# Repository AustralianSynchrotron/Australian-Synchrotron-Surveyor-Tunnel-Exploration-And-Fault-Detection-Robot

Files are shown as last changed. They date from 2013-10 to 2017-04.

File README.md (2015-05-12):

Australian-Synchrotron-Surveyor-Tunnel-Exploration-And-Fault-Detection-Robot
=======

Australian Synchrotron Tunnel Bot


###Requirements
------------

1. Python 2.7.x
2. ZeroMQ 3.2.x
3. pyzmq  13.1.0
4. Pyserial
5. libphidget LATEST (currently 2.1.8.20130723)
6. libusb 1.0-0
7. mjpg-streamer experimental
8. cherrypy 3.2.x
9. Arduino 1.5
-- PS2X by Bill Porter
10. supervisor 3.0b2-1
11. ROOter Huntsman 2014-01-25red

###Changes
-------

ipc doesn't seem to be working on this current configuration (except for LCD screen) so motors and IR Sensors using zmq on tcp://127.0.0.2
ports:
irsensor 127.0.0.2:1000
motors 127.0.0.2:1100

note: srv_motor.py now has the bind command for the motors zmq socket, since it is the service which is always running. If testing run py script with sudo

###Command Line
--------

ssh to odroid. The following command line scripts can be used for some low level control of ass-bot

**move** *\<direction\> \<duration\> \<speed\>*

* direction: forward (f), back (b), left (l), right (r)

* duration: time of movement in seconds

* speed: percentage of max speed. From 1 to 100

**shaft** *\<direction\> \<duration\>*

* direction: up (u) or down (d)

* duration: time of movement in seconds

**camera** *\<direction\> \<PWM duration\>*

* direction: Pan (p) or tilt (t)

* PWM duration: Pulse width from 500 to 2500. Form tilt centre value is 900, for pan centre value is 1500

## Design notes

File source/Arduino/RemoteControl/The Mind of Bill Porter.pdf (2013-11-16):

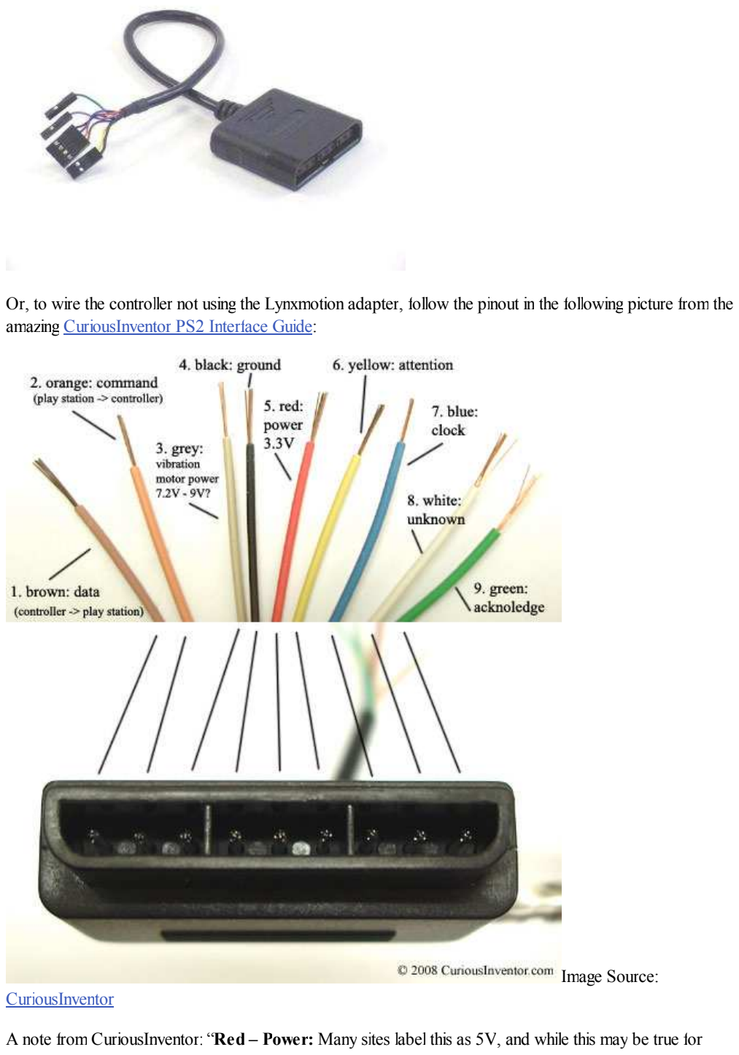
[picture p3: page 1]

Or, to wire the controller not using the Lynxmotion adapter, follow the pinout in the following picture from the amazing CuriousInventor PS2 Interface Guide:

Image Source:
CuriousInventor
A note from CuriousInventor: “Red – | Power: | Many sites label this as 5V, and while this may be true for

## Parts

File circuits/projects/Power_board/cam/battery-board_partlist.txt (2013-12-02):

Partlist

Exported from battery_board.brd at 2/12/2013 4:05:52 PM

EAGLE Version 6.4.0 Copyright (c) 1988-2013 CadSoft

Assembly variant: 

Part         Value           Package              Library  Position (mil)        Orientation

BATT1_V      1-HOLE          1-HOLE_BIG           parts    (3250 3200)           R0
BATT2_V      1-HOLE          1-HOLE_BIG           parts    (2450 3200)           R0
BATTERY1     12V             SCREWTERMINAL-5MM-2  parts    (3900 3600)           R180
BATTERY2     12V             SCREWTERMINAL-5MM-2  parts    (3050 3600)           R180
C1           10uF            C050-024X044         parts    (875 2250)            R180
C2           2.2uF           C050-024X044         parts    (875 2750)            R180
CHARGER      24V             SCREWTERMINAL-5MM-2  parts    (4950 3600)           R180
CHARGE_ON    1-HOLE          1-HOLE_BIG           parts    (5150 2875)           R0
D1           BZX55           DO35Z10              parts    (4500 2350)           R0
D1-12V       30A             TO22-DIODE-H         parts    (3650 1150)           R270
D2-12V       30A             TO22-DIODE-H         parts    (1500 3325)           R270
D3-24V       30A             TO22-DIODE-H         parts    (2500 1150)           R270
FUSE-M1      3A              SCREWTERMINAL-5MM-2  parts    (375 1300)            R270
FUSE-M2      3A              SCREWTERMINAL-5MM-2  parts    (375 1775)            R270
LED-12V                      LED5MM               parts    (5150 1800)           R0
LED-24V                      LED5MM               parts    (5150 1450)           R0
LED-CHARGE                   LED5MM               parts    (5150 2550)           R0
LED-CHARGING                 LED5MM               parts    (5150 2150)           R0
MOBO+5V      2-HOLESSC3.81MM SCREWTERMINAL-3.81MM parts    (250 2550)            R270
MOTOR-1      2-HOLESSC5MM    SCREWTERMINAL-5MM-2  parts    (1850 300)            R0
MOTOR-2      2-HOLESSC5MM    SCREWTERMINAL-5MM-2  parts    (950 300)             R0
OUTPUT       3-HOLE          SCREWTERMINAL-5MM-3  parts    (3500 250)            R0
R1           560R            0309/15              parts    (4600 2150)           R180
R2           1k              0309/15              parts    (4600 1450)           R0
R3           560R            0309/15              parts    (4600 1800)           R0
R4           1k              0309/15              parts    (4600 2875)           R180
R5           220R            0309/15              parts    (4600 2550)           R180
RELAY        5V              RELAY_RT2            parts    (2750 2200)           R180
RELAY_ON     1-HOLE          1-HOLE_BIG           parts    (3250 2575)           R0
VR-MB        LT323A          TO220V-HEATSINK      parts    (1425 2500)           R270

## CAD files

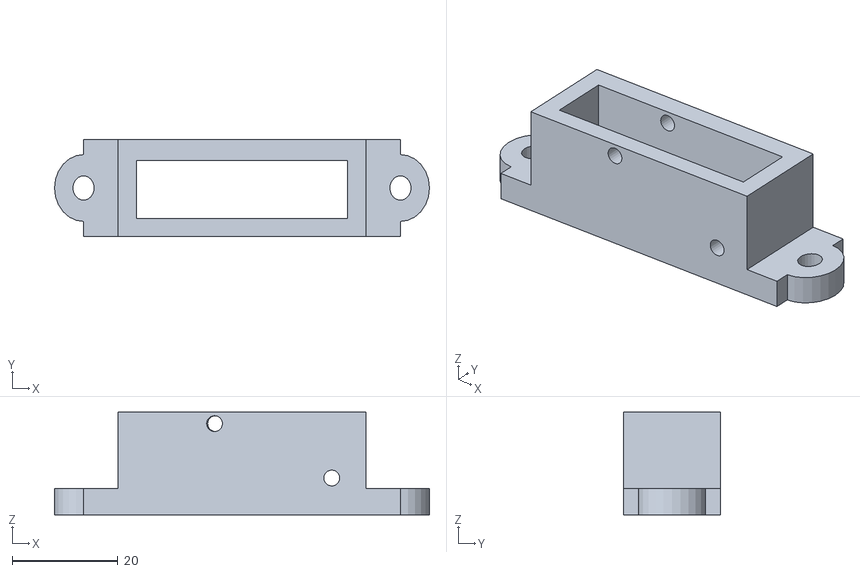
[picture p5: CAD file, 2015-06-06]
drawings/3D_Parts/switch-holder.stl
71.0 x 18.4 x 19.5

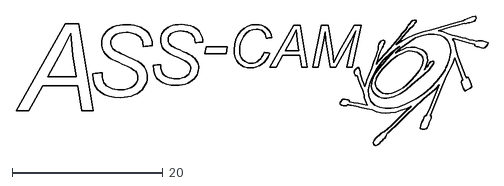
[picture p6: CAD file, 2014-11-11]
drawings/logos/asscam_logo-outline-small.dxf
62.6 x 17.2

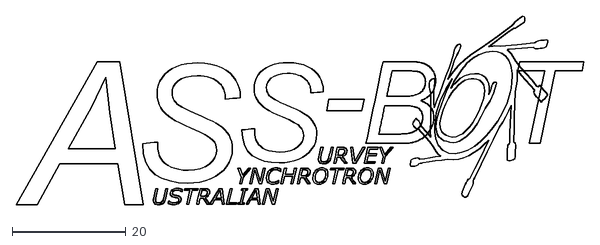
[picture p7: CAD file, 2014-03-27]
drawings/logos/assbot_logo-outline-small.dxf
99.9 x 33.1

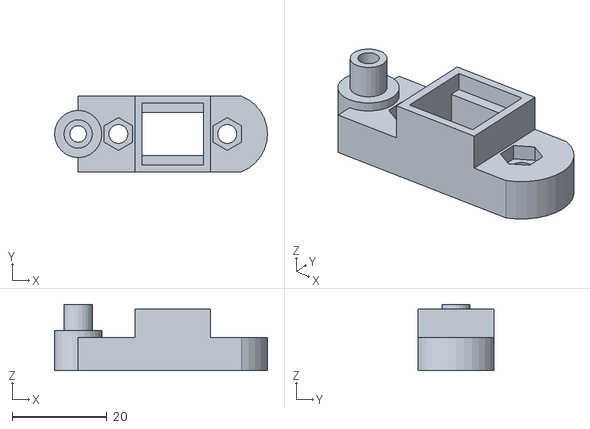
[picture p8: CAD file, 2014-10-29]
drawings/3D_Parts/switch_holder-single.stl
45.0 x 16.0 x 14.0

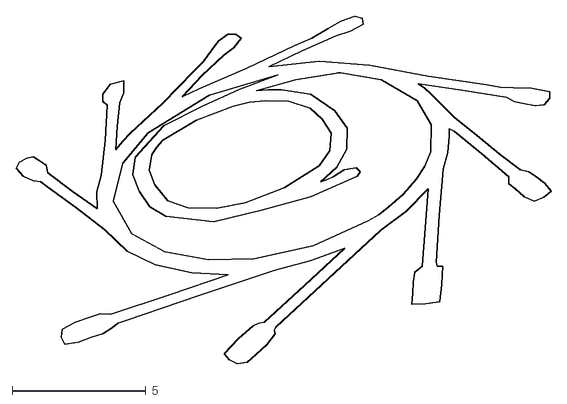
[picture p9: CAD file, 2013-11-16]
drawings/logos/synch-logo-small.dxf
20.0 x 13.0

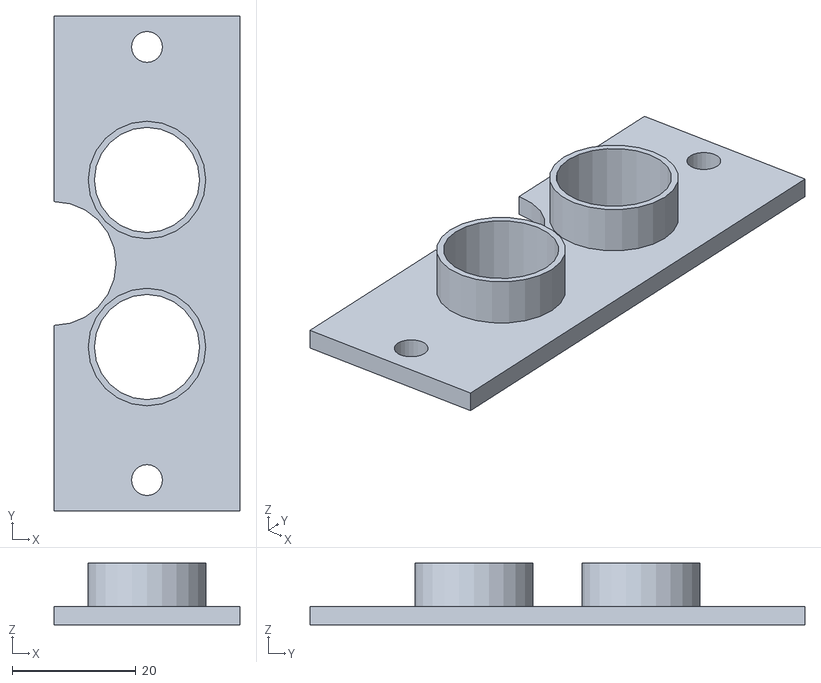
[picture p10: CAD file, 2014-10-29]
drawings/3D_Parts/Ultrasound-mount-cutaway.stl
30.0 x 80.0 x 10.00

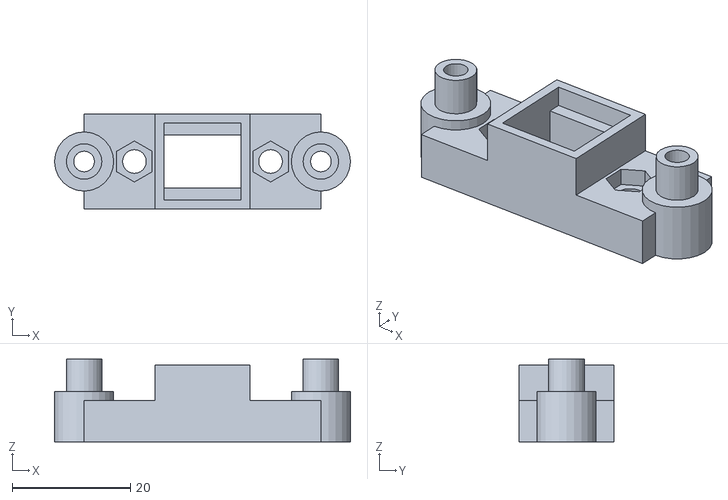
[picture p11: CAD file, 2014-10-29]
drawings/3D_Parts/switch_holder-double.stl
50.0 x 16.0 x 14.0

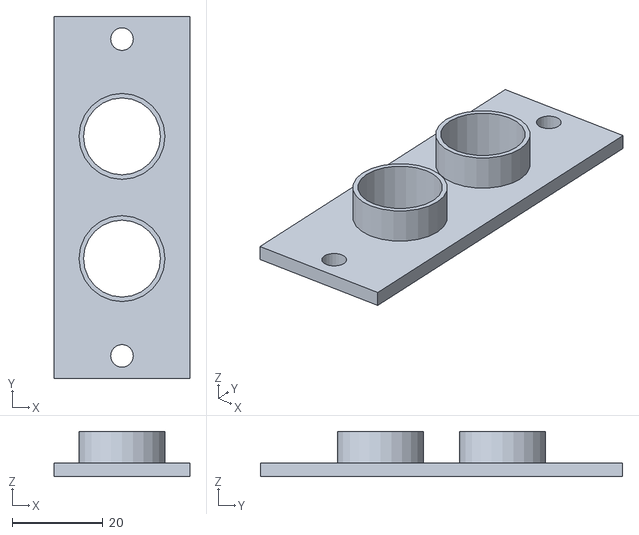
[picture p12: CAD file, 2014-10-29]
drawings/3D_Parts/Ultrasound-mount.stl
30.0 x 80.0 x 10.00

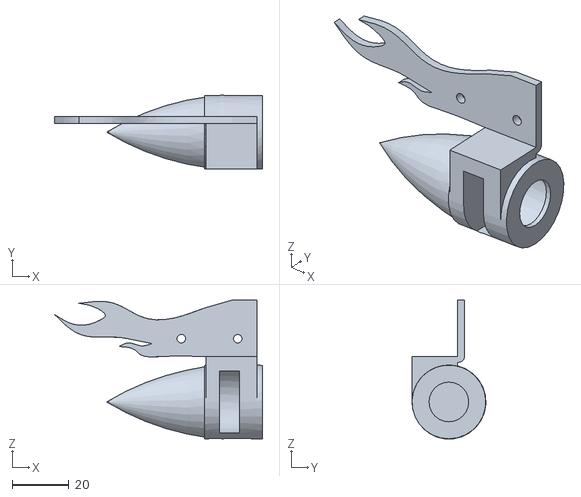
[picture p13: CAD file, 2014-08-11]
drawings/3D_Parts/SnapMagnetV2_Normal.stl
73.4 x 26.1 x 49.0

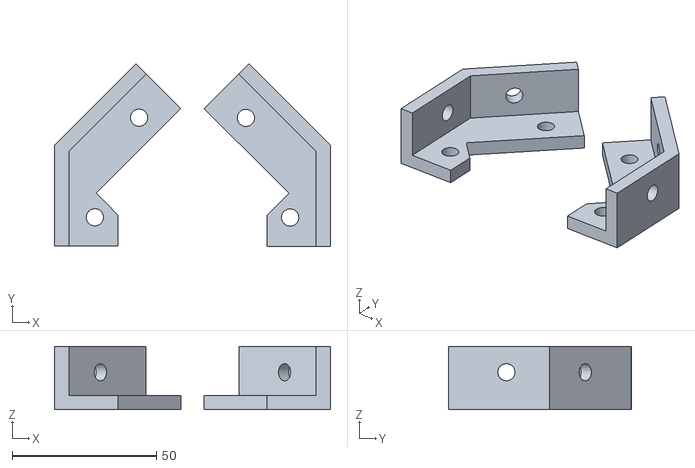
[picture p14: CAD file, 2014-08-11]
drawings/3D_Parts/corner-45deg-back-back.stl
95.7 x 63.4 x 22.0

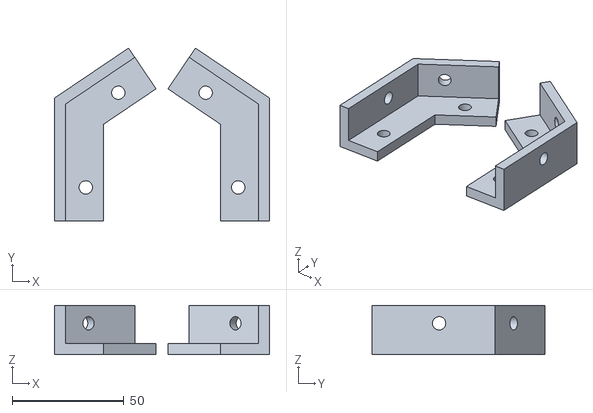
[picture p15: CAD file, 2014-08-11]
drawings/3D_Parts/Corner_pair-36deg.stl
96.2 x 77.4 x 22.0

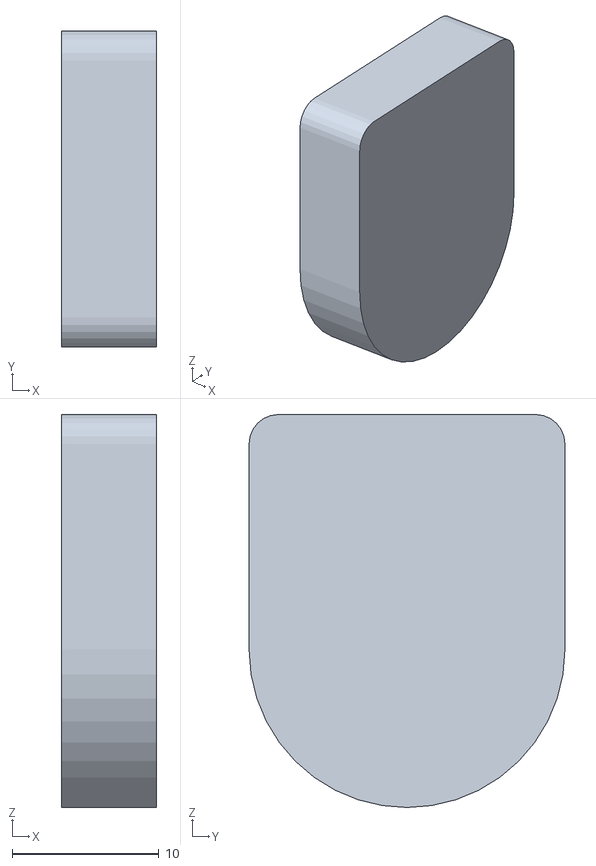
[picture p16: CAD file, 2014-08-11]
drawings/3D_Parts/SnapMagnet_Cork.stl
6.50 x 21.5 x 26.8

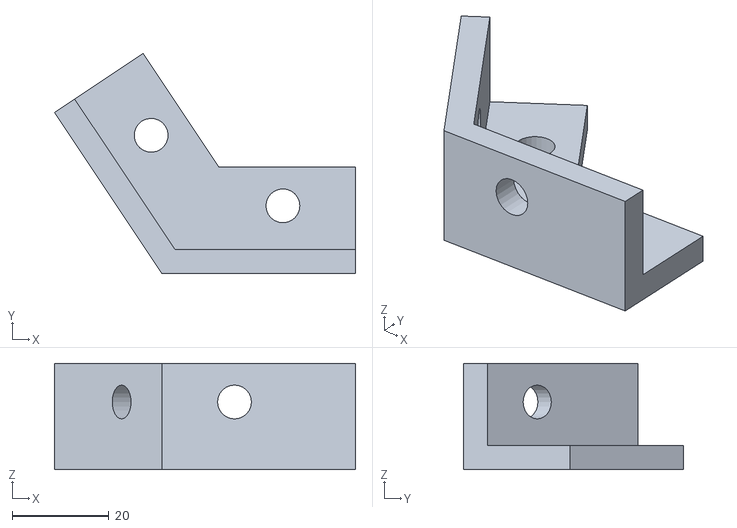
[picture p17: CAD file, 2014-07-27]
drawings/3D_Parts/corner_join_56.stl
62.2 x 45.5 x 22.0

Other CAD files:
drawings/Design/Cover Pieces ACAD2010.dwg
drawings/3D_Parts/Top_Plate_Concept.dwg
drawings/3D_Parts/PanTilt_Metal.dwg
drawings/3D_Parts/SnapMagnetV2_Goofy.stl
drawings/3D_Parts/SnapMagnet.dwg
drawings/3D_Parts/12mm-square-quadangle.skp
drawings/3D_Parts/12mm-square-tripleangle_left.skp
drawings/3D_Parts/12mm-square-tripleangle_left.stl
drawings/3D_Parts/12mm-square-tripleangle_right.skp
drawings/3D_Parts/12mm-square-tripleangle_right.stl
drawings/3D_Parts/20-210-M4-Extrusion.stl
drawings/3D_Parts/20-25angle-bracket-cutaway_left.skp
drawings/3D_Parts/20-25angle-bracket-cutaway_left.stl
drawings/3D_Parts/20-25angle-bracket-cutaway_right.skp
drawings/3D_Parts/20-25angle-bracket-cutaway_right.stl
drawings/3D_Parts/20-25angle-bracket.skp
drawings/3D_Parts/20-M4-connector.stl
drawings/3D_Parts/Calibration.stl
drawings/3D_Parts/Calibration2.stl
drawings/3D_Parts/Fan_Clip.dwg
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

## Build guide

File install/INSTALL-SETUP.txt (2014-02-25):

sudo dpkg-reconfigure tzdata
sudo apt-get remove chrome gimp xbmc
sudo apt-get autoremove
cd ~
mkdir GitHub
cd GitHub
git clone https://github.com/AustralianSynchrotron/Australian-Synchrotron-Surveyor-Tunnel-Exploration-And-Fault-Detection-Robot.git ./ass-bot
cd ~
sudo apt-get install libzmq3 libzmq3-dev
sudo apt-get install python-pip python2.7-dev
sudo pip install pyzmq
sudo apt-get install libusb-1.0-0-dev
mkdir phidgets
cd phidgets
wget http://www.phidgets.com/downloads/libraries/libphidget.tar.gz
tar -zxvf libphidget.tar.gz
cd libphidget-2.1.8.20130723/
./configure
make
sudo make install
wget http://www.phidgets.com/downloads/libraries/PhidgetsPython.zip
unzip PhidgetsPython.zip
cd PhidgetsPython/
sudo python setup.py install
cd ~
sudo pip install cherrypy
*************************************************************************
*  http://forum.odroid.com/viewtopic.php?f=21&t=20
*  Slow network Errors... smsc95xx eth0: kevent 2 may have been dropped
sudo echo 'vm.min_free_kbytes = 65536' >> /etc/sysctl.conf
sudo sysctl -p
sudo echo 'smsc95xx turbo_mode=N' >> /etc/modules 
*************************************************************************
sudo apt-get install subversion libv4l-dev libjpeg8-dev imagemagick
mkdir mjpeg-streamer
svn checkout svn://svn.code.sf.net/p/mjpg-streamer/code/
cd code/mjpg-streamer-experimental/
make USE_LIBV4L2=true clean all
sudo make DESTDIR=/usr install
sudo apt-get install sysstat

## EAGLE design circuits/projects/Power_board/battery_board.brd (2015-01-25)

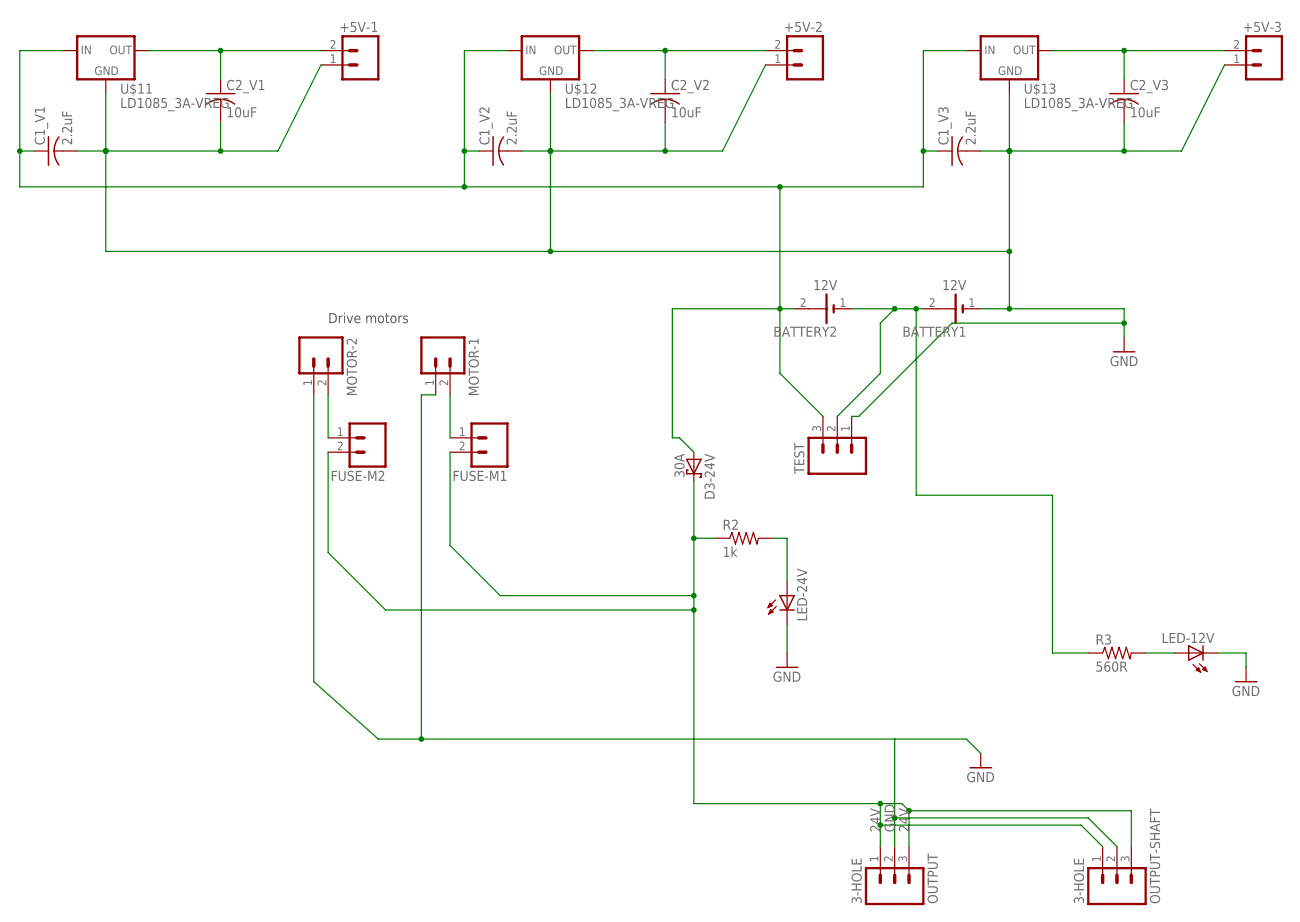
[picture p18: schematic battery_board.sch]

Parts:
+5V-1, +5V-2, +5V-3: 2-HOLESSC3.81MM; SCREWTERMINAL-3.81MM
BATTERY1, BATTERY2: 12V; SCREWTERMINAL-5MM-2
C1_V1, C1_V2, C1_V3: 2.2uF; C050-024X044
C2_V1, C2_V2, C2_V3: 10uF; C050-024X044
D3-24V: 30A; TO22-DIODE-H
FUSE-M1, FUSE-M2: 3A; SCREWTERMINAL-5MM-2
LED-12V, LED-24V: LED-5MM; LED5MM
MOTOR-1, MOTOR-2: 2-HOLESSC5MM; SCREWTERMINAL-5MM-2
OUTPUT: 3-HOLE; SCREWTERMINAL-5MM-3@1
OUTPUT-SHAFT: 3-HOLE; SCREWTERMINAL-5MM-3@1
R2: 1k; 0309/15
R3: 560R; 0309/15
TEST: M03PTH; 1X03
U$11, U$12, U$13: LD1085_3A-VREG; TO220V-HEATSINK2

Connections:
12V: BATTERY2.2 (+), C1_V1.1, C1_V2.1, C1_V3.1, D3-24V.P$1 (A), TEST.3, U$11.3 (IN), U$12.3 (IN), U$13.3 (IN)
24V: D3-24V.P$2 (C), FUSE-M1.2, FUSE-M2.2, OUTPUT.1, OUTPUT.3, OUTPUT-SHAFT.1, OUTPUT-SHAFT.3, R2.1
GND: +5V-1.1, +5V-2.1, +5V-3.1, BATTERY1.1 (-), C1_V1.2, C1_V2.2, C1_V3.2, C2_V1.2, C2_V2.2, C2_V3.2, LED-12V.K (C), LED-24V.K (C), MOTOR-1.1, MOTOR-2.1, OUTPUT.2, OUTPUT-SHAFT.2, TEST.1, U$11.1 (GND), U$12.1 (GND), U$13.1 (GND)
unnamed: LED-24V.A, R2.2
unnamed: BATTERY1.2 (+), BATTERY2.1 (-), R3.1, TEST.2
unnamed: +5V-3.2, C2_V3.1, U$13.2 (OUT)
unnamed: FUSE-M2.1, MOTOR-2.2
unnamed: FUSE-M1.1, MOTOR-1.2
unnamed: LED-12V.A, R3.2
unnamed: +5V-2.2, C2_V2.1, U$12.2 (OUT)
unnamed: +5V-1.2, C2_V1.1, U$11.2 (OUT)

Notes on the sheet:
Drive motors

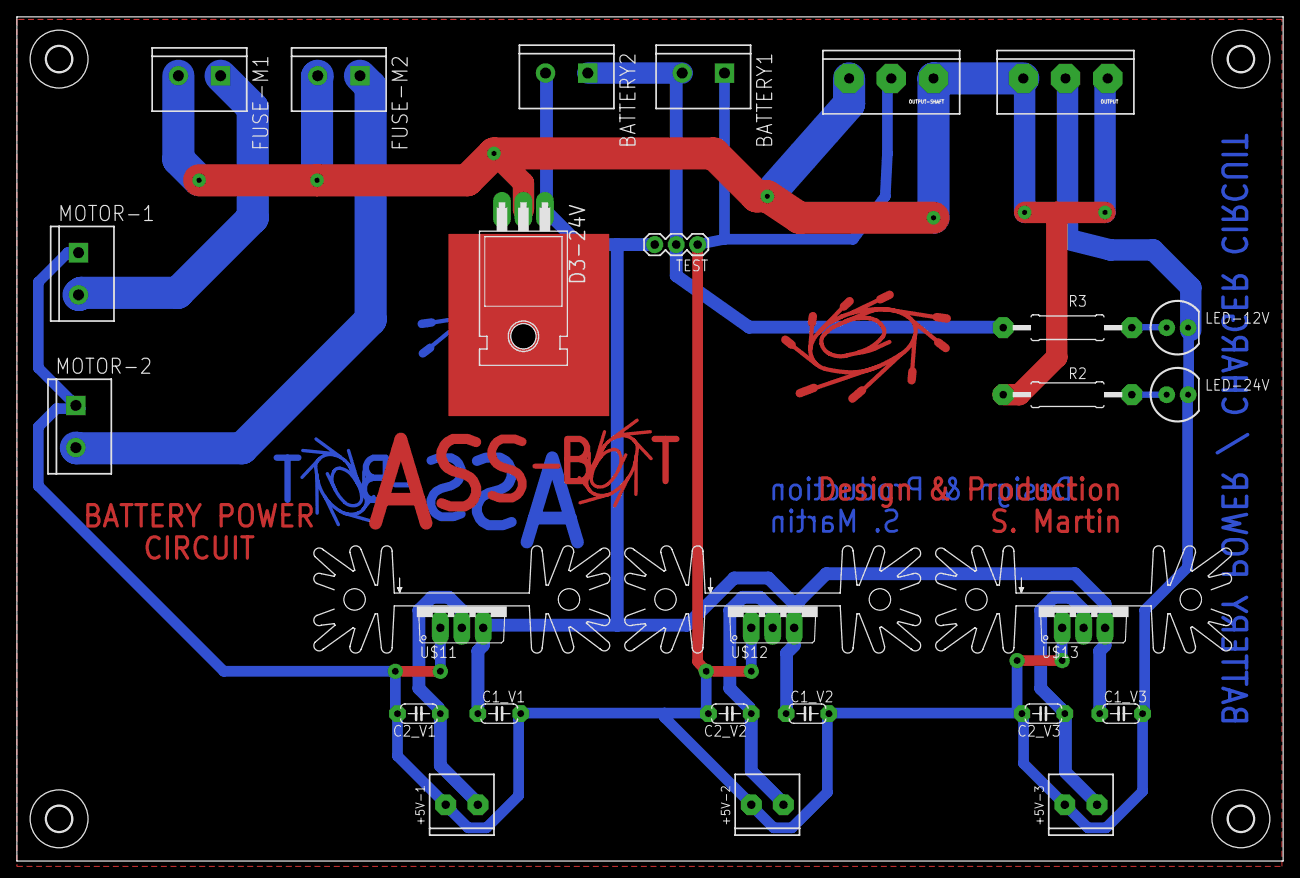
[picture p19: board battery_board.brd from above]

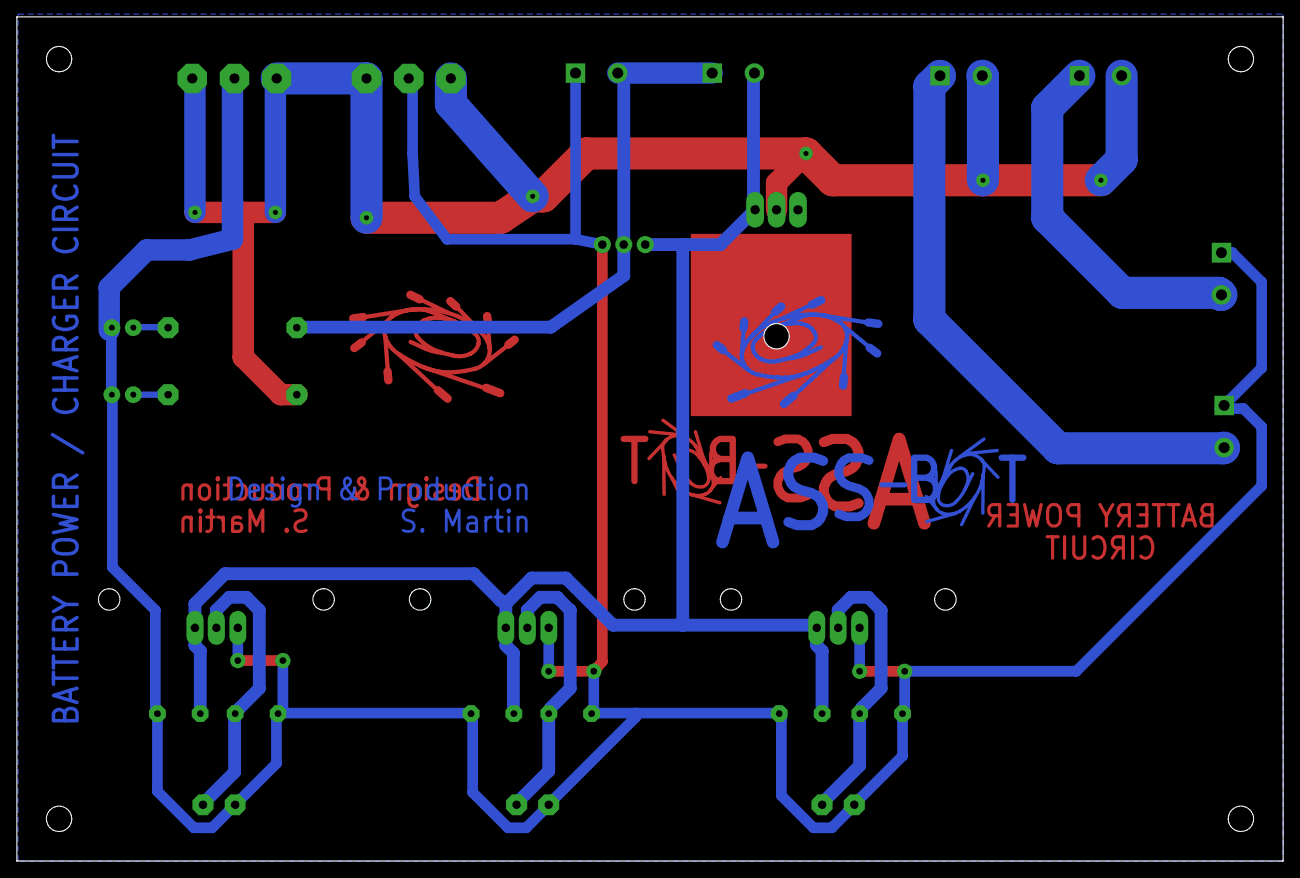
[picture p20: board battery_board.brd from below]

Board: 2 copper layers, 150.0 x 100.0 mm, 36 parts (2 on the bottom side), 11 nets.

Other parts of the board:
U$1, U$8: LOGO-SYNCHROTRON
U$2: LOGO-ASSBOT-SILK
U$3, U$4, U$5, U$6: 3,0
U$7, U$9: LOGO-ASSBOT
U$10: LOGO-SYNCHROTRON-SILK

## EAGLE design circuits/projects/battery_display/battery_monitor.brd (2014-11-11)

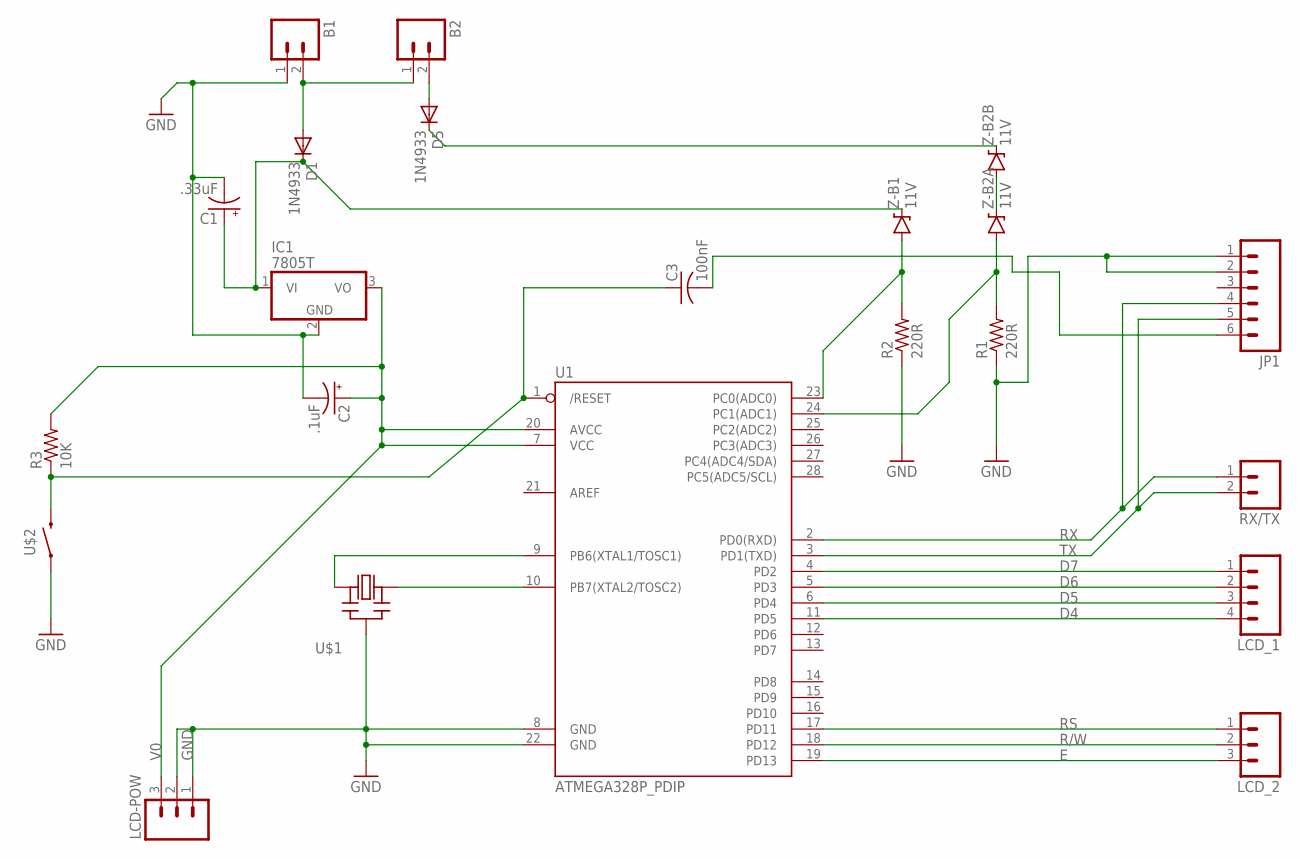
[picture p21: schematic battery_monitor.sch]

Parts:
B1, B2: 2-HOLES2-HOLES-5.08MM; 2-HOLES_BIG
C1: .33uF; E2,5-5
C2: .1uF; E2,5-5
C3: 100nF; C050-025X075
D1, D5: 1N4933; DO41-10
IC1: 7805T; TO220H
JP1: M06LONGPADS; 1X06_LONGPADS
LCD-POW: M03PTH; 1X03
LCD_1: M04PTH; 1X04
LCD_2: M03PTH; 1X03
R1, R2: 220R; 0207/10
R3: 10K; 0207/10
RX/TX: M02PTH; 1X02
U1: ATMEGA328P_PDIP; DIL28-3
U$1: OSCILLATOR-THM; CERM_OSC
U$2: SWITCH-MOMENTARY4MM; TACTILE_SWITCH_SMD
Z-B1, Z-B2A, Z-B2B: 11V; DIODE-ZENER

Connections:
D4: LCD_1.4, U1.11 (PD5)
D5: LCD_1.3, U1.6 (PD4)
D6: LCD_1.2, U1.5 (PD3)
D7: LCD_1.1, U1.4 (PD2)
E: LCD_2.3, U1.19 (PD13)
GND: B1.1, C1.-, C2.-, IC1.2 (GND), JP1.1, JP1.2, LCD-POW.1, LCD-POW.2, R1.1, R2.1, U1.8 (GND), U1.22 (GND), U$1.P$2 (GND), U$2.1, U$2.2 (1)
unnamed: U1.10 (PB7(XTAL2/TOSC2)), U$1.P$3 (OUT)
unnamed: U1.9 (PB6(XTAL1/TOSC1)), U$1.P$1 (IN)
unnamed: B1.2, B2.1, D1.A
unnamed: C1.+, D1.C, IC1.1 (VI), Z-B1.P$1 (C)
unnamed: Z-B2A.P$1 (C), Z-B2B.P$2 (A)
unnamed: C3.1, R3.1, U1.1 (/RESET), U$2.3 (2), U$2.4 (2)
unnamed: C3.2, JP1.6
unnamed: R2.2, U1.23 (PC0(ADC0)), Z-B1.P$2 (A)
unnamed: R1.2, U1.24 (PC1(ADC1)), Z-B2A.P$2 (A)
unnamed: D5.C, Z-B2B.P$1 (C)
unnamed: B2.2, D5.A
R/W: LCD_2.2, U1.18 (PD12)
RS: LCD_2.1, U1.17 (PD11)
RX: JP1.4, RX/TX.1, U1.2 (PD0(RXD))
TX: JP1.5, RX/TX.2, U1.3 (PD1(TXD))
V0: C2.+, IC1.3 (VO), LCD-POW.3, R3.2, U1.7 (VCC), U1.20 (AVCC)

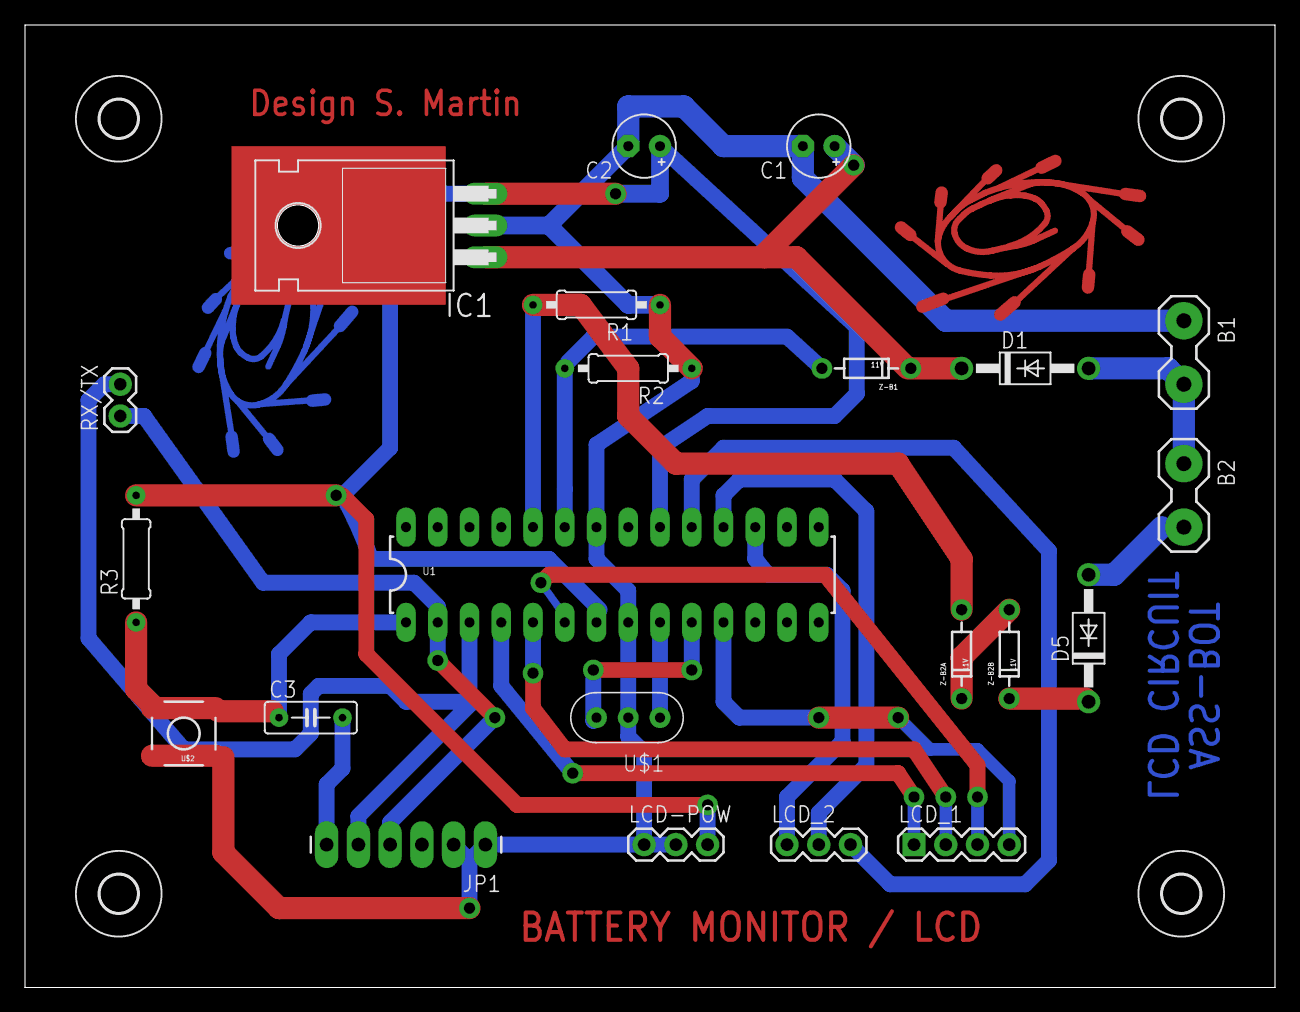
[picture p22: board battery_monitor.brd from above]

Board: 2 copper layers, 100.0 x 77.0 mm, 28 parts (1 on the bottom side), 22 nets.

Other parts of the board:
U$3, U$4, U$5, U$6: 3,0
U$7, U$8: LOGO-SYNCHROTRON

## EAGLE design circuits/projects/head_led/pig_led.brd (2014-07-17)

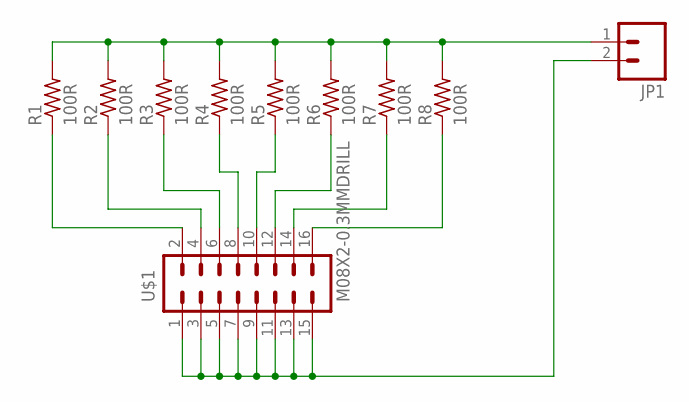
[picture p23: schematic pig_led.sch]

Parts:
JP1: M023.5MM; SCREWTERMINAL-3.5MM-2
R1, R2, R3, R4, R5, R6, R7, R8: 100R; 0207/10
U$1: M08X2-0.3MMDRILL; 2X8

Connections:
GND: JP1.2, U$1.1, U$1.3, U$1.5, U$1.7, U$1.9, U$1.11, U$1.13, U$1.15
unnamed: R1.1, U$1.2
unnamed: R2.1, U$1.4
unnamed: R3.1, U$1.6
unnamed: R4.1, U$1.8
unnamed: R5.1, U$1.10
unnamed: R6.1, U$1.12
unnamed: R7.1, U$1.14
unnamed: R8.1, U$1.16
VCC: JP1.1, R1.2, R2.2, R3.2, R4.2, R5.2, R6.2, R7.2, R8.2

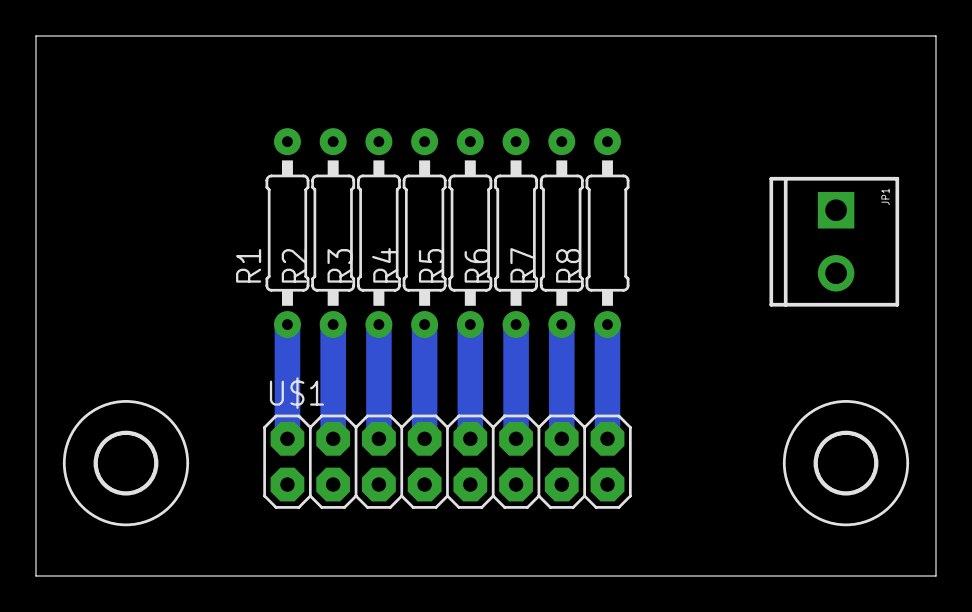
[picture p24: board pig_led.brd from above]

Board: 2 copper layers, 50.0 x 30.0 mm, 12 parts (0 on the bottom side), 10 nets.

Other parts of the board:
U$2, U$3: 3,2

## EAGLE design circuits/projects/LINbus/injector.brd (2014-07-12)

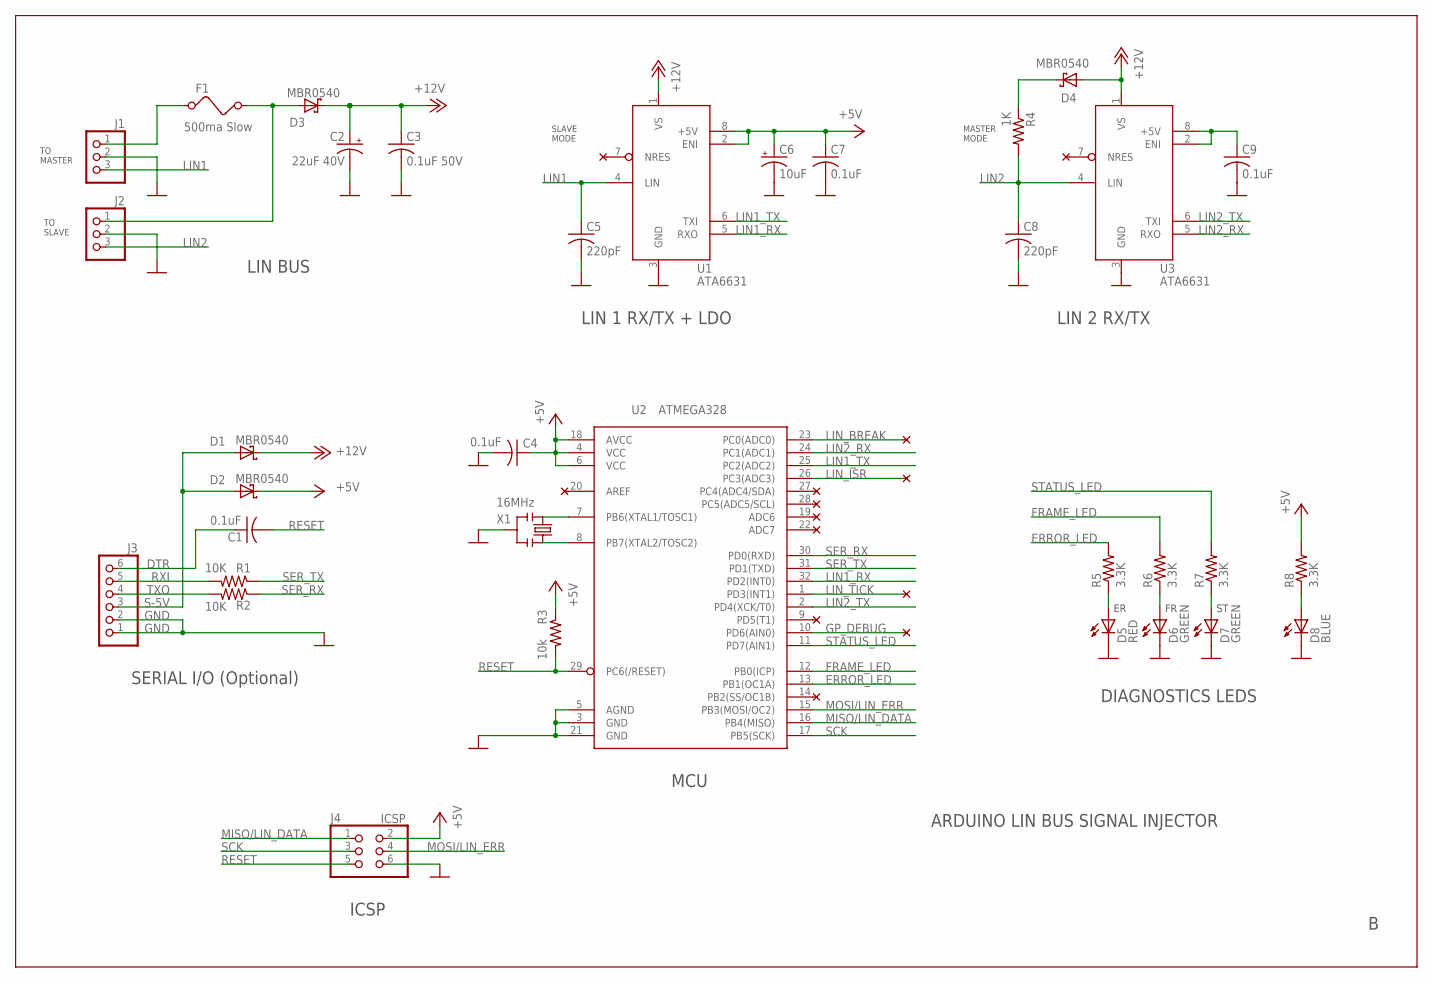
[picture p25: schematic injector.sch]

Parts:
C1, C4, C7, C9: 0.1uF; C0805
C2: 22uF 40V; UD-6,3X5,8_NICHICON
C3: 0.1uF 50V; C0805
C5, C8: 220pF; C0805
C6: 10uF; A/3216-18R
D1, D2, D3, D4: MBR0540; SOD123FL
D5: RED; 1206-LED
D6, D7: GREEN; 1206-LED
D8: BLUE; 1206-LED
F1: 500ma Slow; 1206
J1, J2: PINHD-1X3; 1X03
J3: PINHD-1X6; 1X06
J4: ICSP; 2X03
R1, R2: 10K; R0805
R3: 10k; R0805
R4: 1K; R0805
R5, R6, R7, R8: 3.3K; R0805
U1, U3: ATA6631; SO-08
U2: ATMEGA328; TQFP32-08
X1: 16MHz; RESONATOR-SMD

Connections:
+5V: C4.1, C6.+, C7.1, D2.C, J4.2, R3.1, R8.2, U1.2 (ENI), U1.8 (+5V), U2.4 (VCC), U2.6 (VCC), U2.18 (AVCC)
+12V: C2.+, C3.1, D1.C, D3.C, D4.A, U1.1 (VS), U3.1 (VS)
DTR: C1.1, J3.6
ERROR_LED: R5.2, U2.13 (PB1(OC1A))
FRAME_LED: R6.2, U2.12 (PB0(ICP))
GND: C2.-, C3.2, C4.2, C5.2, C6.-, C7.2, C8.2, C9.2, D5.C, D6.C, D7.C, D8.C, J1.2, J2.2, J3.1, J3.2, J4.6, U1.3 (GND), U2.3 (GND), U2.5 (AGND), U2.21 (GND), U3.3 (GND), X1.2
GP_DEBUG: U2.10 (PD6(AIN0))
LIN1: C5.1, J1.3, U1.4 (LIN)
LIN1_RX: U1.5 (RXO), U2.32 (PD2(INT0))
LIN1_TX: U1.6 (TXI), U2.25 (PC2(ADC2))
LIN2: C8.1, J2.3, R4.2, U3.4 (LIN)
LIN2_RX: U2.24 (PC1(ADC1)), U3.5 (RXO)
LIN2_TX: U2.2 (PD4(XCK/T0)), U3.6 (TXI)
LIN_BREAK: U2.23 (PC0(ADC0))
LIN_ISR: U2.26 (PC3(ADC3))
LIN_TICK: U2.1 (PD3(INT1))
MISO/LIN_DATA: J4.1, U2.16 (PB4(MISO))
MOSI/LIN_ERR: J4.4, U2.15 (PB3(MOSI/OC2))
unnamed: D7.A, R7.1
unnamed: D8.A, R8.1
unnamed: D6.A, R6.1
unnamed: D5.A, R5.1
unnamed: D3.A, F1.2, J2.1
unnamed: D4.C, R4.1
RESET: C1.2, J4.5, R3.2, U2.29 (PC6(/RESET))
RXI: J3.5, R1.2
S-5V: D1.A, D2.A, J3.3
SCK: J4.3, U2.17 (PB5(SCK))
SECONDARY_5V: C9.1, U3.2 (ENI), U3.8 (+5V)
SER_RX: R2.1, U2.30 (PD0(RXD))
SER_TX: R1.1, U2.31 (PD1(TXD))
STATUS_LED: R7.2, U2.11 (PD7(AIN1))
TXO: J3.4, R2.2
VBAT: F1.1, J1.1
XTAL1: U2.7 (PB6(XTAL1/TOSC1)), X1.3
XTAL2: U2.8 (PB7(XTAL2/TOSC2)), X1.1

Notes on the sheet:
LIN BUS
DIAGNOSTICS LEDS
ICSP
LIN 1 RX/TX + LDO
LIN 2 RX/TX
MCU
SERIAL I/O (Optional)
ARDUINO LIN BUS SIGNAL INJECTOR
MASTER MODE
TO MASTER
TO SLAVE
SLAVE MODE

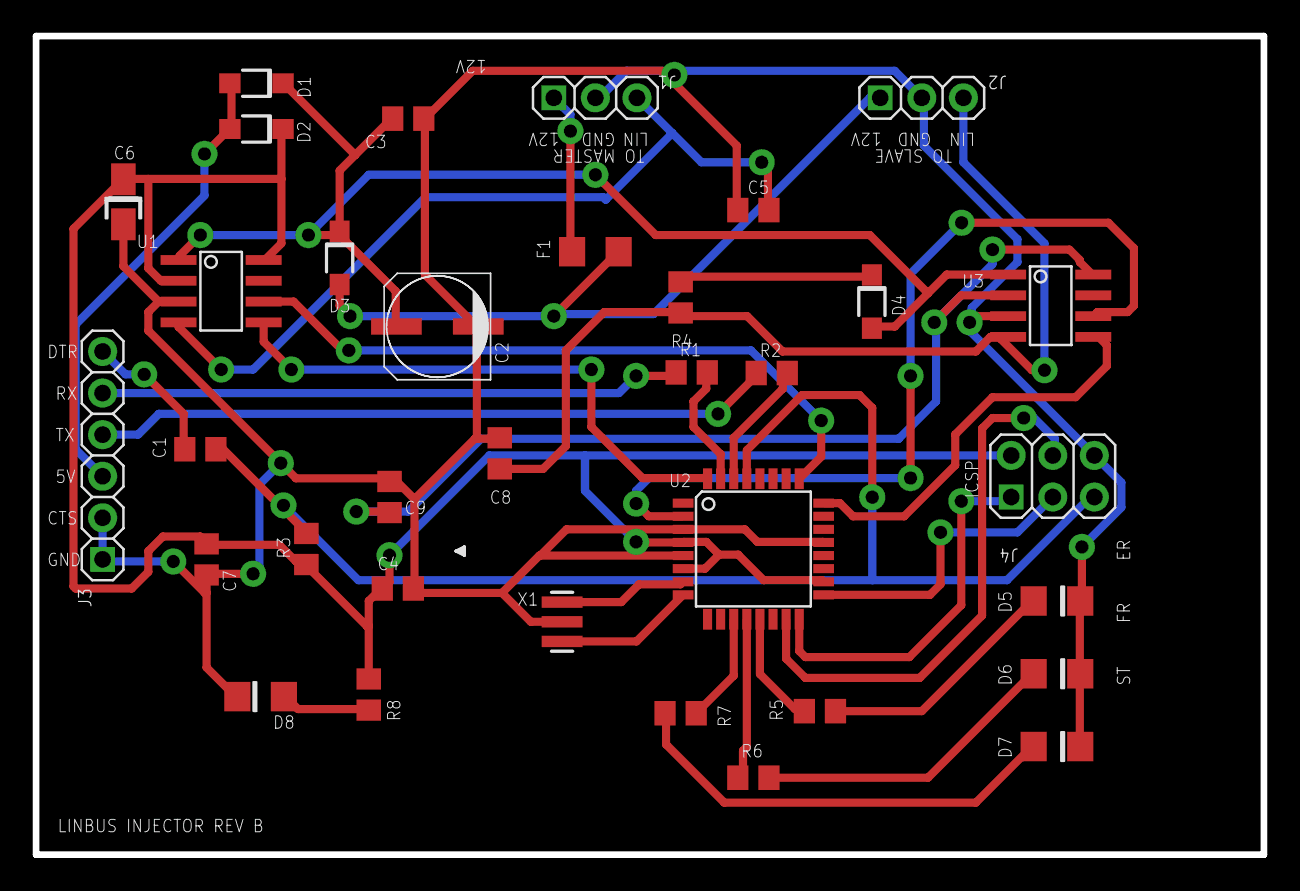
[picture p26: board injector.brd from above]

Board: 2 copper layers, 75.0 x 50.0 mm, 34 parts (0 on the bottom side), 32 nets.

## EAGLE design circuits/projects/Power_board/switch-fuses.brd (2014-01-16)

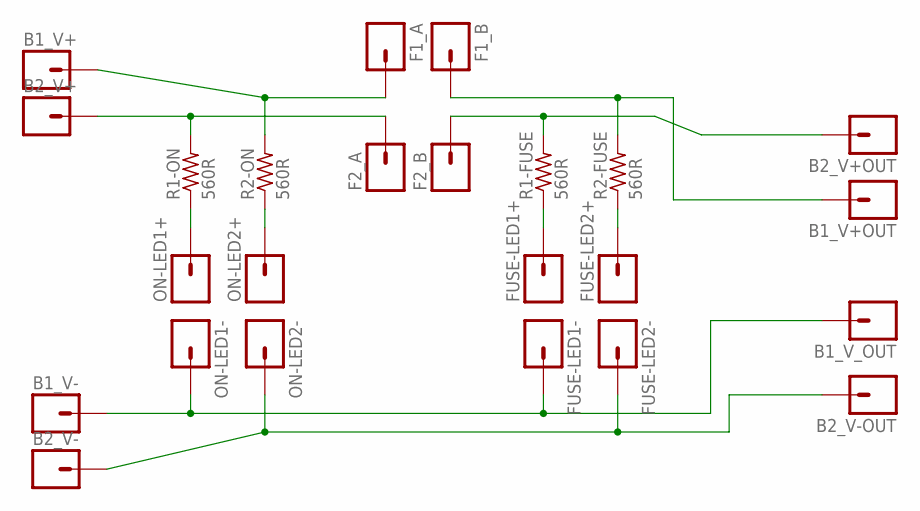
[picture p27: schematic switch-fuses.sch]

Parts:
B1_V+, B1_V+OUT, B1_V-, B1_V_OUT, B2_V+, B2_V+OUT, B2_V-, B2_V-OUT: 1-HOLE2.5MM; 1-HOLE-2.5MM
F1_A, F1_B, F2_A, F2_B: 1-HOLE2.5MM; 1-HOLE-2.5MM
FUSE-LED1+, FUSE-LED1-, FUSE-LED2+, FUSE-LED2-: 1-HOLE0.8MM; 1-HOLE
ON-LED1+, ON-LED1-, ON-LED2+, ON-LED2-: 1-HOLE0.8MM; 1-HOLE
R1-FUSE, R1-ON, R2-FUSE, R2-ON: 560R; 0309/15

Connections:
unnamed: FUSE-LED1+.1, R1-FUSE.1
unnamed: FUSE-LED2+.1, R2-FUSE.1
unnamed: ON-LED1+.1, R1-ON.1
unnamed: ON-LED2+.1, R2-ON.1
V+1: B2_V+OUT.P$1, F2_B.P$1, R1-FUSE.2
V+2: B1_V+OUT.P$1, F1_B.P$1, R2-FUSE.2
V-1: B1_V-.P$1, B1_V_OUT.P$1, FUSE-LED1-.1, ON-LED1-.1
V-2: B2_V-.P$1, B2_V-OUT.P$1, FUSE-LED2-.1, ON-LED2-.1
VIN1: B1_V+.P$1, F1_A.P$1, R2-ON.2
VIN2: B2_V+.P$1, F2_A.P$1, R1-ON.2

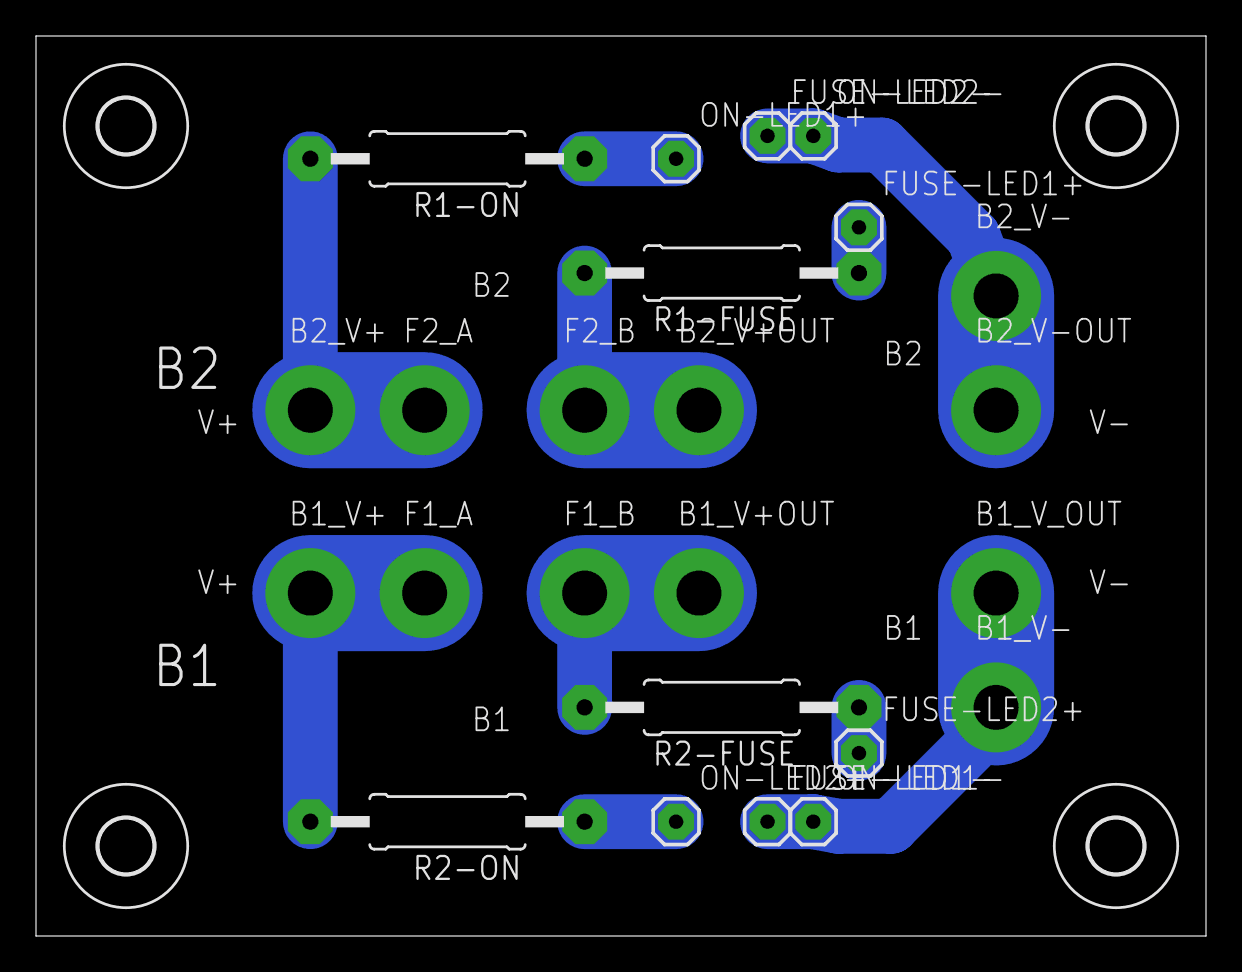
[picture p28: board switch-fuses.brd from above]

Board: 2 copper layers, 65.0 x 50.0 mm, 28 parts (0 on the bottom side), 10 nets.

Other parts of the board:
U$1, U$2, U$3, U$4: 3,0

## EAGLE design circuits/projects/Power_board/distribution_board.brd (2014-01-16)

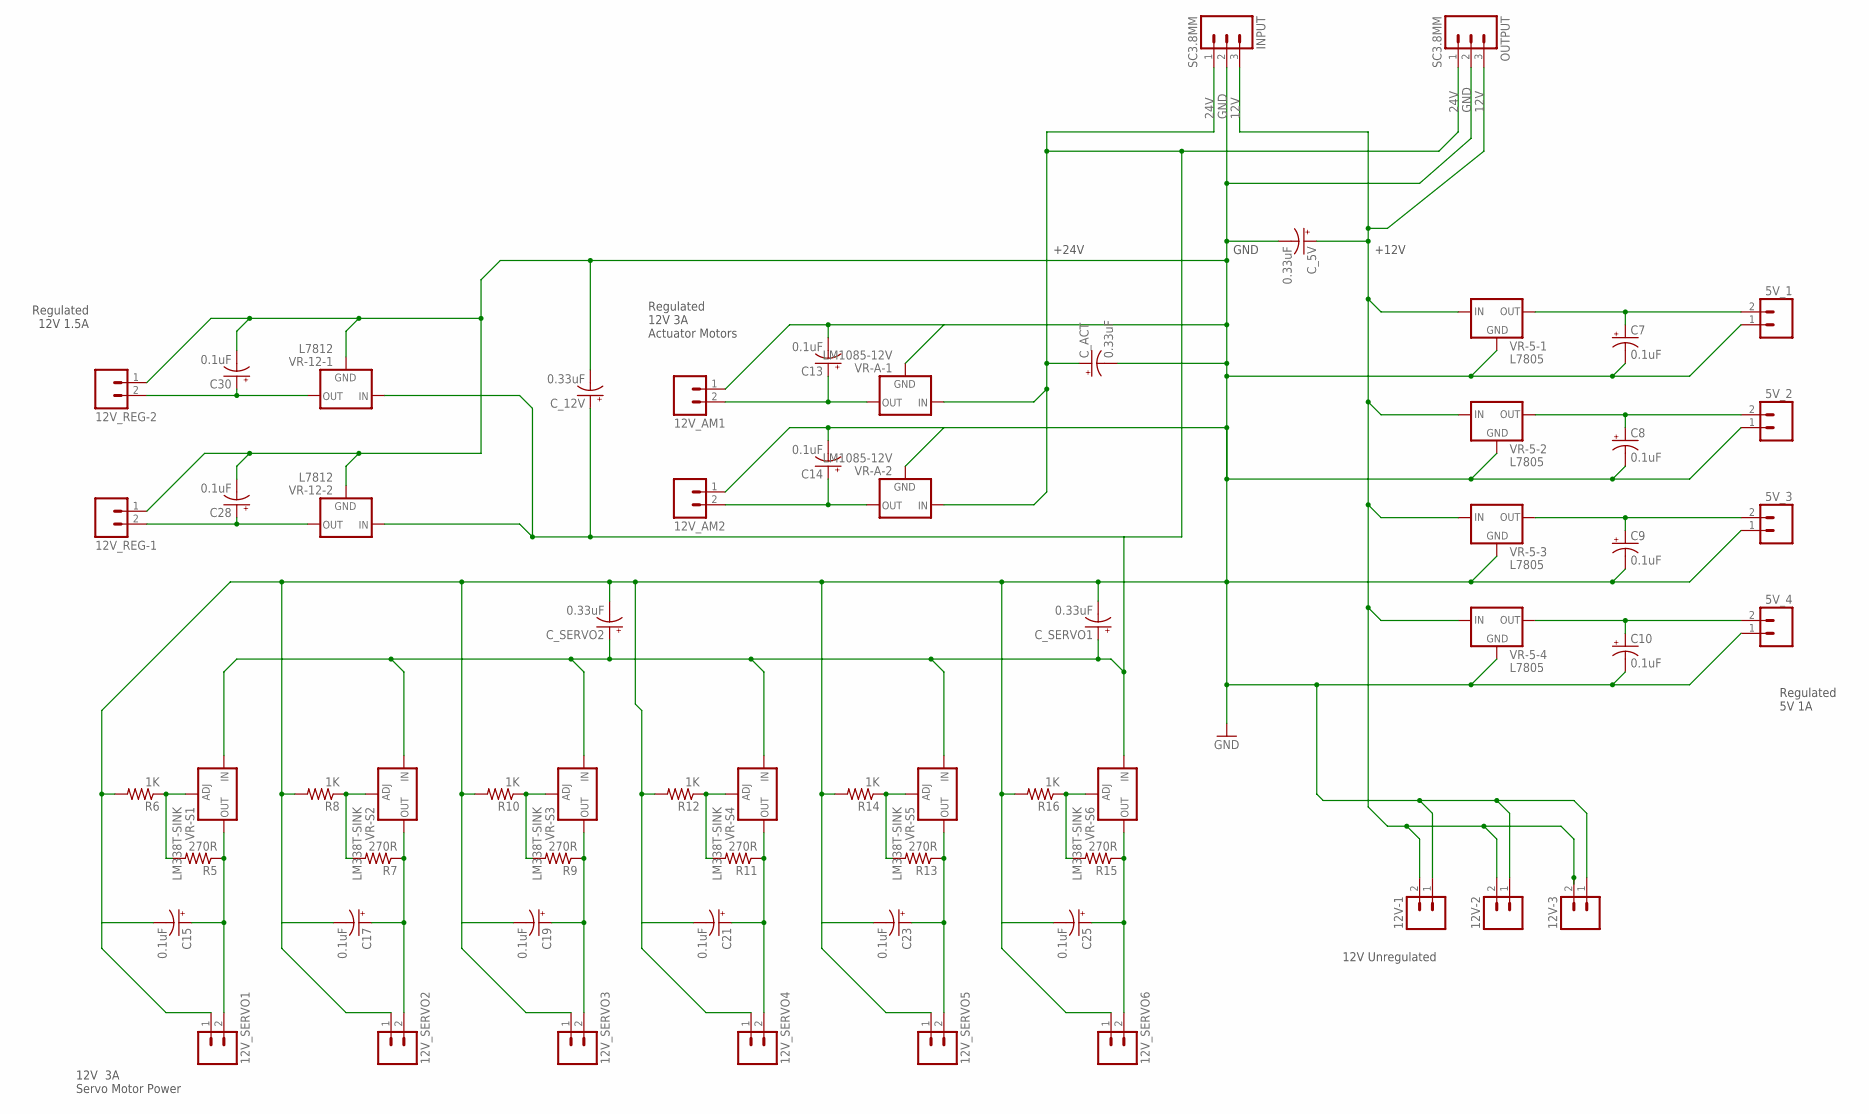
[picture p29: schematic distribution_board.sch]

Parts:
5V_1, 5V_2, 5V_3, 5V_4, 12V-1, 12V-2, 12V-3, 12V_AM1, 12V_AM2, 12V_REG-1, 12V_REG-2, 12V_SERVO1, 12V_SERVO2, 12V_SERVO3, 12V_SERVO4, 12V_SERVO5, 12V_SERVO6: SC3.81MM; SCREWTERMINAL-3.81MM
C7, C8, C9, C10, C13, C14, C15, C17, C19, C21, C23, C25, C28, C30: 0.1uF; E2,5-5
C_5V, C_12V: 0.33uF; E2,5-5
C_ACT: 0.33uF; E2,5-5
C_SERVO1, C_SERVO2: 0.33uF; E2,5-5
INPUT: SC3.8MM; SCREWTERMINAL-5MM-3
OUTPUT: SC3.8MM; SCREWTERMINAL-5MM-3
R5, R7, R9, R11, R13, R15: 270R; 0207/2V
R6, R8, R10, R12, R14, R16: 1K; 0207/2V
VR-5-1, VR-5-2, VR-5-3, VR-5-4: L7805; TO263
VR-12-1, VR-12-2: L7812; TO263
VR-A-1, VR-A-2: LM1085-12V; TO220V-HEATSINK
VR-S1, VR-S2, VR-S3, VR-S4, VR-S5, VR-S6: LM338T-SINK; TO220V-HEATSINK

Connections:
12V: 12V-1.2, 12V-2.2, 12V-3.2, C_5V.+, INPUT.3, OUTPUT.3, VR-5-1.1 (IN), VR-5-2.1 (IN), VR-5-3.1 (IN), VR-5-4.1 (IN)
24V: C_12V.+, C_ACT.+, C_SERVO1.+, C_SERVO2.+, INPUT.1, OUTPUT.1, VR-12-1.1 (IN), VR-12-2.1 (IN), VR-A-1.3 (IN), VR-A-2.3 (IN), VR-S1.3 (IN), VR-S2.3 (IN), VR-S3.3 (IN), VR-S4.3 (IN), VR-S5.3 (IN), VR-S6.3 (IN)
GND: 5V_1.1, 5V_2.1, 5V_3.1, 5V_4.1, 12V-1.1, 12V-2.1, 12V-3.1, 12V_AM1.1, 12V_AM2.1, 12V_REG-1.1, 12V_REG-2.1, 12V_SERVO1.1, 12V_SERVO2.1, 12V_SERVO3.1, 12V_SERVO4.1, 12V_SERVO5.1, 12V_SERVO6.1, C7.-, C8.-, C9.-, C10.-, C13.-, C14.-, C15.-, C17.-, C19.-, C21.-, C23.-, C25.-, C28.-, C30.-, C_5V.-, C_12V.-, C_ACT.-, C_SERVO1.-, C_SERVO2.-, INPUT.2, OUTPUT.2, R6.2, R8.2, R10.2, R12.2, R14.2, R16.2, VR-5-1.3 (GND), VR-5-2.3 (GND), VR-5-3.3 (GND), VR-5-4.3 (GND), VR-12-1.3 (GND), VR-12-2.3 (GND), VR-A-1.1 (GND), VR-A-2.1 (GND)
unnamed: 12V_REG-1.2, C28.+, VR-12-2.2 (OUT)
unnamed: 5V_1.2, C7.+, VR-5-1.2 (OUT)
unnamed: 5V_2.2, C8.+, VR-5-2.2 (OUT)
unnamed: 5V_3.2, C9.+, VR-5-3.2 (OUT)
unnamed: 5V_4.2, C10.+, VR-5-4.2 (OUT)
unnamed: 12V_AM1.2, C13.+, VR-A-1.2 (OUT)
unnamed: 12V_AM2.2, C14.+, VR-A-2.2 (OUT)
unnamed: R5.2, R6.1, VR-S1.1 (ADJ)
unnamed: 12V_REG-2.2, C30.+, VR-12-1.2 (OUT)
unnamed: 12V_SERVO1.2, C15.+, R5.1, VR-S1.2 (OUT)
unnamed: 12V_SERVO2.2, C17.+, R7.1, VR-S2.2 (OUT)
unnamed: R7.2, R8.1, VR-S2.1 (ADJ)
unnamed: 12V_SERVO3.2, C19.+, R9.1, VR-S3.2 (OUT)
unnamed: R9.2, R10.1, VR-S3.1 (ADJ)
unnamed: 12V_SERVO4.2, C21.+, R11.1, VR-S4.2 (OUT)
unnamed: R11.2, R12.1, VR-S4.1 (ADJ)
unnamed: 12V_SERVO5.2, C23.+, R13.1, VR-S5.2 (OUT)
unnamed: R13.2, R14.1, VR-S5.1 (ADJ)
unnamed: 12V_SERVO6.2, C25.+, R15.1, VR-S6.2 (OUT)
unnamed: R15.2, R16.1, VR-S6.1 (ADJ)

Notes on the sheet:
+24V
+12V
GND
Regulated 5V 1A
Regulated 12V 3A Actuator Motors
12V 3A Servo Motor Power
Regulated 12V 1.5A
12V Unregulated


Board: 2 copper layers, 160.0 x 100.0 mm, 72 parts (1 on the bottom side), 23 nets.

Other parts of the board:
U$2, U$4: LOGO-SYNCHROTRON
U$3: LOGO-ASSBOT
U$5: LOGO-ASSBOT-SILK
U$6, U$7, U$8, U$9: 3,0

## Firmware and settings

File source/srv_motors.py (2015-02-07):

#!/usr/bin/env python

""" srv_motors.py: Receive commands to control 2 phidgets motors"""

""" Usage:  create a zmq push socket to send a serialised dictionary
            through ipc:///tmp/motors.ipc 
            The message should be of the form:
            msg = {'leftA': '<int>', 'rightA': '<int>', 'leftV': '<int>', 'rightV': '<int>', ['rel': 'true'] }
"""

"""
Borrowed and modified from the phidgets example code by Adam Stelmack
http://creativecommons.org/licenses/by/2.5/ca/
"""



#Basic imports
from ctypes import *
import sys
#Phidget specific imports
from Phidgets.PhidgetException import PhidgetErrorCodes, PhidgetException
from Phidgets.Events.Events import AttachEventArgs, DetachEventArgs, ErrorEventArgs, CurrentChangeEventArgs, InputChangeEventArgs, VelocityChangeEventArgs
from Phidgets.Devices.MotorControl import MotorControl
#import methods for sleeping thread
from time import sleep

import zmq

import logging
from datetime import datetime

#Create an motorcontrol object
try:
    motorControlL = MotorControl() # Left Motor
    motorControlR = MotorControl() # Right Motor
except RuntimeError as e:
    print("Runtime Exception: %s" % e.details)
    print("Exiting....")
    exit(1)

#Information Display Function
def displayDeviceInfo():
    print("|------------|------------------------------------|--------------|------------|")
    print("|- Attached -|-              Type                -|- Serial No. -|-  Version -|")
    print("|------------|------------------------------------|--------------|------------|")
    print("|- %8s -|- %30s -|- %10d -|- %8d -|" % (motorControlL.isAttachedToServer(), motorControlL.getDeviceName(), motorControlL.getSerialNum(), motorControlL.getDeviceVersion()))
    print("|- %8s -|- %30s -|- %10d -|- %8d -|" % (motorControlR.isAttachedToServer(), motorControlR.getDeviceName(), motorControlR.getSerialNum(), motorControlR.getDeviceVersion()))
    print("|------------|------------------------------------|--------------|------------|")

#Event Handler Callback Functions
def motorControlAttached(e):
    attached = e.device
    print("MotorControl %i Attached!" % (attached.getSerialNum()))

def motorControlDetached(e):
    detached = e.device
    print("MotorControl %i Detached!" % (detached.getSerialNum()))

def motorControlError(e):
    try:
        source = e.device
        print("Motor Control %i: Phidget Error %i: %s" % (source.getSerialNum(), e.eCode, e.description))
    except PhidgetException as e:
        print("Phidget Exception %i: %s" % (e.code, e.details))

def motorControlCurrentChanged(e):
    source = e.device
    print("Motor Control %i: Motor %i Current Draw: %f" % (source.getSerialNum(), e.index, e.current))

def motorControlInputChanged(e):
    source = e.device
    print("Motor Control %i: Input %i State: %s" % (source.getSerialNum(), e.index, e.state))

def motorControlVelocityChanged(e):
    source = e.device
    print("Motor Control %i: Motor %i Current Velocity: %f" % (source.getSerialNum(), e.index, e.velocity))

#Main Program Code
#try:
#    motorControlL.setOnAttachHandler(motorControlAttached)
#    motorControlL.setOnDetachHandler(motorControlDetached)
#    motorControlL.setOnErrorhandler(motorControlError)
#    motorControlL.setOnCurrentChangeHandler(motorControlCurrentChanged)
#    motorControlL.setOnInputChangeHandler(motorControlInputChanged)
#    motorControlL.setOnVelocityChangeHandler(motorControlVelocityChanged)

#    motorControlR.setOnAttachHandler(motorControlAttached)
#    motorControlR.setOnDetachHandler(motorControlDetached)
#    motorControlR.setOnErrorhandler(motorControlError)
#    motorControlR.setOnCurrentChangeHandler(motorControlCurrentChanged)
#    motorControlR.setOnInputChangeHandler(motorControlInputChanged)
#    motorControlR.setOnVelocityChangeHandler(motorControlVelocityChanged)

#except PhidgetException as e:
#    print("Phidget Exception %i: %s" % (e.code, e.details))
#    print("Exiting....")
#    exit(1)

print("Opening phidget object on Phidgets WebService 'odroid'...")

try:
    #motorControlL.openPhidget(serial=298857)
    #motorControlR.openPhidget(serial=298856)
    motorControlL.openRemote('odroid',serial=298857)
    motorControlR.openRemote('odroid',serial=298856)
except PhidgetException as e:
    print("Phidget Exception %i: %s" % (e.code, e.details))
    print("Exiting....")
    exit(1)

if not motorControlL.isAttachedToServer():
    sleep(2)

print('motorControlL attached to server status: %s' % motorControlL.isAttachedToServer() )
print('motorControlR attached to server status: %s' % motorControlR.isAttachedToServer() )

print("Waiting for attach....")

try:
    motorControlL.waitForAttach(10000)
    motorControlR.waitForAttach(10000)
except PhidgetException as e:
    print("Phidget Exception %i: %s" % (e.code, e.details))
    try:
        motorControlL.closePhidget()
        motorControlR.closePhidget()
    except PhidgetException as e:
        print("Phidget Exception %i: %s" % (e.code, e.details))
        print("Exiting....")
        exit(1)
    print("Exiting....")
    exit(1)
else:
    displayDeviceInfo()

#print(motorControlL.getAccelerationMin(0))
#print(motorControlR.getAccelerationMin(0))
#print(motorControlL.getAccelerationMax(0))
#print(motorControlR.getAccelerationMax(0))

#no good for automation scripts...
#print("Press Enter to continue....")
#chr = sys.stdin.read(1)

Amax = motorControlL.getAccelerationMax(0)
Amin = motorControlL.getAccelerationMin(0)
print("minimum acceleration = %f, maximum acceleration = %f" % ( Amin, Amax))

context = zmq.Context()
motors_receiver = context.socket(zmq.PULL)
motors_receiver.bind("ipc:///tmp/motors.ipc")
#motors_receiver.bind("tcp://127.0.0.2:1100")

#battery_socket = context.socket(zmq.PUB)
#battery_socket.bind("ipc:///tmp/battery.ipc")

bumper_reciever = context.socket(zmq.SUB)
bumper_reciever.connect("ipc://tmp/bumper.ipc")

# messages passed in as {left acc, left vel, right acc, right vel, rel}
# velocity: -100 to 100; 0 is stop
# acceleration: AccMin(24.51) to AccMax (6250)
# rel: relative or absolute settings

while True:

    #bat1 = motorControlL.getSupplyVoltage()
    #bat2 = motorControlR.getSupplyVoltage()
    #print("Battery1: %s, Battery2: %s" % (bat1, bat2))
    #msg = {'battery1': bat1, 'battery2': bat2}
    #battery_socket.send_json(msg)

    print("Going into forever loop mode")
    result = motors_receiver.recv_json()
    print(result)

    if 'rel' in result:
        print("Relative Settings...")
        try:
            lar = motorControlL.getAcceleration(0)
            rar = motorControlR.getAcceleration(0)

            lvr = motorControlL.getAcceleration(0)
            rvr = motorControlR.getAcceleration(0)
        except PhidgetException as e:
            print("Phidget Exception %i: %s" % (e.code, e.details))

        try:
            motorControlL.setAcceleration(0, (int(result['leftA']) + lar) )
            motorControlR.setAcceleration(0, (int(result['rightA']) + rar) )
            motorControlL.setVelocity(0, (int(result['leftV']) + lvr) )
            motorControlR.setVelocity(0, (int(result['rightV']) + rvr) )
        except PhidgetException as e:
            print("Phidget Exception %i: %s" % (e.code, e.details))

    else:
        print("Absolute Settings...")
	print("%s :: leftV = %s, rightV = %s, leftA = %s, rightA = %s" % (str(datetime.now()),result['leftV'],result['rightV'],result['leftA'],result['rightA']) )
        #fix bad accelearation values
	if result['leftA'] < Amin:
		leftA = Amax
	elif result['leftA'] > Amax:
		leftA = Amax
	else:
		leftA = result['leftA']
	if result['rightA'] < Amin:
		rightA = Amax
	elif result['rightA'] > Amax:
		rightA = Amax
	else:
		rightA = result['rightA']
	print("leftA = %f, rightA = %f" % ( leftA, rightA))	
        #logging.debug('Received: %s, %s, %s, %s' % (result['leftA'],result['rightA'],result['leftV'],result['rightV']))
        try:
            motorControlL.setAcceleration(0, leftA)#int(result['leftA']))
            motorControlR.setAcceleration(0, rightA)#int(result['rightA']))
            motorControlL.setVelocity(0, int(result['leftV']))
            motorControlR.setVelocity(0, int(result['rightV']))
        except PhidgetException as e:
            print("BanG: Phidget Exception %i: %s" % (e.code, e.details))
    
#Control the motor a bit.
#print("Will now simulate motor operation....")
#print("Step 1: increase acceleration to 50, set target speed at 100")
#try:
#    motorControlL.setAcceleration(0, 50.00)
#    motorControlR.setAcceleration(0, 50.00)
#    motorControlL.setVelocity(0, 100.00)
#    motorControlR.setVelocity(0, 100.00)
#    sleep(5) #sleep for 5 seconds
#except PhidgetException as e:
#    print("Phidget Exception %i: %s" % (e.code, e.details))

#print("Step 2: Set acceleration to 100, decrease target speed to 75")
#try:
#    motorControlL.setAcceleration(0, 100.00)
#    motorControlL.setVelocity(0, 75.00)
#    sleep(5) #sleep for 5 seconds
#except PhidgetException as e:
#    print("Phidget Exception %i: %s" % (e.code, e.details))

#print("Step 3: Stop the motor by decreasing speed to 0 at 50 acceleration")
#try:
#    motorControlL.setAcceleration(0, 50.00)
#    motorControlL.setVelocity(0, 0.00)
#    sleep(5) #sleep for 5 seconds
#except PhidgetException as e:
#    print("Phidget Exception %i: %s" % (e.code, e.details))
#else:
#    try:
#        motorControlL.setAcceleration(0, 1.00)
#    except PhidgetException as e:
#        print("Phidget Exception %i: %s" % (e.code, e.details))

print("Press Enter to quit....")

chr = sys.stdin.read(1)

print("Closing...")

try:
    motorControlL.closePhidget()
    motorControlR.closePhidget()
except PhidgetException as e:
    print("Phidget Exception %i: %s" % (e.code, e.details))
    print("Exiting....")
    exit(1)

print("Done.")
exit(0)

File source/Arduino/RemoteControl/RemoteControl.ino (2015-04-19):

//#include <Dhcp.h>
//#include <Dns.h>
#include <SPI.h>
#include <Ethernet.h>
#include <EthernetClient.h>
//#include <EthernetServer.h>
//#include <EthernetUdp.h>

#include <PS2X_lib.h>

PS2X ps2x;

int error = 0; 
byte type = 0;
byte vibrate = 55;

byte mac[] = {0x00, 0xDE, 0xFA, 0xCE, 0xD0, 0x69};
//byte ip[] = {10, 6, 0, 230}; //arduino fixed IP if dhcp fails
//byte gateway[] = {10, 6, 0, 254};
//byte subnet[] = {255, 255, 0, 0};
IPAddress ip(10, 6, 0, 230); //arduino fixed IP if dhcp fails
IPAddress gateway(10, 6, 0, 254);
IPAddress subnet(255, 255, 0, 0);
//IPAddress server(10, 6, 0, 17); //connection server
IPAddress server(10, 3, 1, 68); //connection server - Office Network
EthernetClient client;
int port = 8080;

void setup() {
  // put your setup code here, to run once:
  Serial.begin(57600);
  
  
  error = ps2x.config_gamepad(7,5,6,8, true, true);   //setup pins and settings:  
 //GamePad(clock, command, attention, data, Pressures?, Rumble?) check for error
 //Looks like data needds to be on a PWM output
 //Pin Colours and Ports:
 //  Data:    Black:    8
 //  Command: Brown:    5
 //  Attn:    Green:    6
 //  Clk:     Blue:     7
 //  Power:   Yellow:   3v3
 //  Gnd:     Orange:   gnd
 //  Vibe:    Red:      5v0
 
  if(error == 0){
   //Serial.println("Found Controller, configured successful");
  }
   
  else if(error == 1)
   Serial.println("No controller found, check wiring, see readme.txt to enable debug. visit www.billporter.info for troubleshooting tips");
   
  else if(error == 2)
   Serial.println("Controller found but not accepting commands. see readme.txt to enable debug. Visit www.billporter.info for troubleshooting tips");
   
  else if(error == 3)
   Serial.println("Controller refusing to enter Pressures mode, may not support it. ");
   
  type = ps2x.readType(); 
     switch(type) {
       case 0:
        Serial.println("Unknown Controller type");
       break;
       case 1:
        Serial.println("DualShock Controller Found");
       break;
       case 2:
         Serial.println("GuitarHero Controller Found");
       break;
     }
     
  // give the ethernet module time to boot up:
  delay(1000);
  
  Serial.println("Connecting to ASS-Bot...");
  if( Ethernet.begin(mac) == 0)
  {
    //Serial.println("Failed to configure Ethernet using DHCP");
    Ethernet.begin(mac, ip);
  }
  Serial.println(Ethernet.localIP());
  delay(1000);
  
  //client.connect(server, port);
  
}

//int tmp = 0;

void loop() {
  // put your main code here, to run repeatedly: 
  if(error == 1) //skip loop if no controller found
    return;
    
  ps2x.read_gamepad(false, vibrate);
  
  //Use start button to exit program... reset to start
  //if(ps2x.Button(PSB_START))
  //  return;
    
  // Left analogue stick to control robot movements
  // Right analogue stick to control peripheral movements
  // Using select to switch between peripherals
  // Control pad to raise and lower platform...
  
  String controlString = "";
  
  controlString+="Rx=";
  controlString+=ps2x.Analog(PSS_RX); //analog joystick right
  controlString+="&Ry=";
  controlString+=ps2x.Analog(PSS_RY);
  controlString+="&Lx=";
  controlString+=ps2x.Analog(PSS_LX); //analog joystick left
  controlString+="&Ly=";
  controlString+=ps2x.Analog(PSS_LY);
  controlString+="&BtnX=";
  controlString+=ps2x.Analog(PSAB_BLUE); //analog reading of button X
  controlString+="&BtnUp=";
  controlString+=ps2x.Button(PSB_PAD_UP); //up button on control pad, don't care about force
  controlString+="&BtnDn=";
  controlString+=ps2x.Button(PSB_PAD_DOWN); //down button on control pad, don't care about force
  controlString+="&Mode=Arduino";
  
//  Serial.println(ps2x.Analog(PSS_LY),DEC);
//  Serial.println(ps2x.Analog(PSS_RY),DEC);
//  controlString+="&tempInt=";
//  controlString+=tmp;
  
//  tmp+= 1;
  
  Serial.println(controlString);
  sendData(controlString);
  
  //if(ps2x.Button(PSS_LY))
  //{
  //  Serial.print("Left Analog");
  //  Serial.print(ps2x.Analog(PSS_LY),DEC); //Y-axis
  //  Serial.print(":");
  //  Serial.print(ps2x.Analog(PSS_LX),DEC); //X-axis
  //}
  
  //delay(1000);
}

void sendData(String myData)
{
  //Serial.print("Preparing to send html data: ");
  //Serial.println(myData);
  // if there's a successful connection:
  
  int state = client.connect(server, port);
  //int state = client.connected();
  //Serial.println(state);
  
  if ( state ) {
    //Serial.println("connecting...");
    // send the HTTP PUT request:
    client.println("POST /control HTTP/1.1");
    client.println("Host: 10.6.0.4");
    client.println("From: RemoteControl");
    client.println("User-Agent: Arduino/1.5");
    client.println("Connection: close");  
    client.println("Content-Type: application/x-www-form-urlencoded"); 
    client.print("Content-Length: ");
    client.println(myData.length());

    // last pieces of the HTTP PUT request:
    client.println();
    // here's the actual content of the PUT request:
    client.println(myData);
    client.println();
    
    //Serial.println("Message sent...");
    
    client.stop();
  } 
  else {
    // if you couldn't make a connection:
    Serial.println("connection failed");

    //if no connection, restart the connection
    //Serial.println("Restarting connection.");
      // give the ethernet module time to boot up:

    client.stop();
    //client.flush();
    //client.connect(server, port);
    delay(100);
  }
  
}

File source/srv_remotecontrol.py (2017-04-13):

import cherrypy
import zmq
import math
import os
import simplejson as json

context = zmq.Context()
motors_socket = context.socket(zmq.PUSH)
#motors_socket = context.socket(zmq.PUB)
motors_socket.connect("ipc:///tmp/motors.ipc") #Not supported by windows, comment out for testing
#motors_socket.connect("tcp://127.0.0.2:1100")
#motors_socket.connect("tcp://localhost:8558") # Comment out for production

battery_socket = context.socket(zmq.SUB)
battery_socket.connect("ipc:///tmp/battery.ipc")
battery_socket.setsockopt(zmq.SUBSCRIBE, "") #subscribe all messages

HTML_DIR = os.path.join(os.path.dirname(os.path.abspath(__file__)), 'html/')

class RemoteControl(object):
    neutral_max = 155
    neutral_min = 100
    neutral = 128
    v_max = 100
    v_min = -100

    @cherrypy.expose
    def index(self):
        print HTML_DIR
        #return "ASS-Bot Remote Control Home Page<p><img src='http://10.3.1.199:8090/?action=stream' width = '720'/>"
        #return "ASS-Bot Remote Control Home Page<p><img src='http://10.3.1.103:8090/?action=stream'/>"
        return open(os.path.join(HTML_DIR, 'control.html'))
        # Use for web page control

    @cherrypy.expose
    def batteries(self):
        msg = battery_socket.recv_json()
        #print("Battery1: %s, Battery2: %s" ( msg['battery1'],msg['battery2'] ))
        print(msg)
        return json.dumps(msg)

    @cherrypy.expose
    def control(self, **kws):
        print HTML_DIR
        # if no message is received the set position to neutral, 0 acceleration
        lx = ly = rx = ry = self.neutral
        accel = 0

        print(kws)
        if "Mode" in kws:
            mode = str(kws['Mode'])
        if "Lx" in kws:
            lx = int(kws['Lx'])
        if "Ly" in kws:
            ly = int(kws['Ly'])
        if "Rx" in kws:
            rx = int(kws['Rx'])
        if "Ry" in kws:
            ry = int(kws['Ry'])
        if "BtnX" in kws:
            accel = int(kws['BtnX'])
        if "Sel" in kws:
            sel = int(kws['Sel'])

        print("Received... leftH:%s leftV:%s rightH:%s rightV:%s speed:%s" % (lx, ly, rx, ry, accel))

        # Left stick controls vehicle base movement
        # Right stick auxilary device control
        # - use select button to change between devices
        # X Button (blue) motor acceleration / enable movement
        # dead band around neutral analog stick position +/-10units

        #convert coordinate system 0 - 128
        #convert to a number between 0 and 100 or 0 and -100 for reverse.

        #conversion from the arduino/ps2 controller
        #print("Checking for Arduino control...")
        if mode == "Arduino":
            print("Arduino in control")
            quad = self.which_quadrant(lx,ly)

            if quad == 1:
                leftV = self.v_max
                lfx = lx - self.neutral
                lfy = self.neutral - ly
                tmpDeg = math.degrees(math.atan2(lfy,lfx))
                rightV = (tmpDeg / 90) * self.v_max

            elif quad == 2:
                rightV = self.v_max
                lfx = self.neutral - lx
                lfy = self.neutral - ly
                tmpDeg = math.degrees(math.atan2(lfy,lfx))
                leftV = (tmpDeg / 90) * self.v_max

            elif quad == 3:
                rightV = self.v_min
                lfx = self.neutral - lx
                lfy = ly - self.neutral
                tmpDeg = math.degrees(math.atan2(lfy,lfx))
                leftV = (tmpDeg / 90) * self.v_min

            elif quad == 4:
                leftV = self.v_min
                lfx = lx - self.neutral
                lfy = ly - self.neutral
                tmpDeg = math.degrees(math.atan2(lfy,lfx))
                rightV = (tmpDeg / 90) * self.v_min

            elif quad == 5:
                leftV = self.v_min
                rightV = self.v_max

            elif quad == 6:
                leftV = self.v_max
                rightV = self.v_min

            else:  #neutral
                leftV = 0
                rightV = 0

        #leftA = rightA = accel
        leftA = rightA = 50  # 25%/s^2 change in velocity requests

        msg = {'leftA': leftA, 'rightA': rightA, 'leftV': leftV, 'rightV': rightV}
        #Send the zmq message tothe motor server
        motors_socket.send_json(msg)
        print("Message sent... leftMotor:%s rightMotor:%s" % (leftV, rightV))

        return "Received... leftH:%s leftV:%s rightH:%s rightV:%s" % (lx, ly, rx, ry)

    def which_quadrant(self, horiz, vert):
        quad = 0
        print("vert:%s  horiz:%s" % (horiz, vert))
        if ((horiz > self.neutral) and (vert < self.neutral)):
            quad = 1	# ahead right
            print("Quad 1  vert:%s  horiz:%s" % (horiz, vert))
        if ((horiz < self.neutral) and (vert < self.neutral)):
            quad = 2	# ahead left
            print("Quad 2  vert:%s  horiz:%s" % (horiz, vert))
        if ((horiz < self.neutral) and (vert > self.neutral)):
            quad = 3	# behind left
            print("Quad 3  vert:%s  horiz:%s" % (horiz, vert))
        if ((horiz > self.neutral) and (vert > self.neutral)):
            quad = 4	# behind right
            print("Quad 4  vert:%s  horiz:%s" % (horiz, vert))
        if ((horiz < 20) and (vert > 115) and (vert < 140)):
            quad = 5
            print("Spin Left!")
        if ((horiz > 230) and (vert > 115) and (vert <140)):
            quad = 6
            print("Spin Right!")
        if ((horiz > self.neutral_min) and (horiz < self.neutral_max) and (vert > self.neutral_min) and (vert < self.neutral_max)):
            quad = 0	# overwrite the neutral square
            print("Quad 0  vert:%s  horiz:%s" % (horiz, vert))

        return quad

cherrypy.config.update({
    #'server.socket_host': '10.3.1.199',
    #'server.socket_host': '10.6.0.17', #uncomment for windows box testing
    #'server.socket_host': '10.3.1.103',
    #'server.socket_host': '10.6.0.177',
    #'server.socket_host': '10.3.1.236',
    #'server.socket_host': '10.3.1.173',
    'server.socket_host': '0.0.0.0',
    'server.socket_port': 8080
})

config = {'/':
        {'tools.staticdir.debug': True,
         'log.screen': True
        },
    '/html':
        {'tools.staticdir.on': True,
         'tools.staticdir.dir': HTML_DIR,
        }
    }

#cherrypy.quickstart(RemoteControl())
#cherrypy.engine.subscribe('start', open_page)
cherrypy.tree.mount(RemoteControl(), '/', config = config)
cherrypy.engine.start()

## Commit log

2013-10-20 Changed motor mount method
    [20130808_AssBot-Mechanical.dwg]
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2013-11-06 made eagle library for circuit board
    [power_board.brd, power_board.sch]
2013-11-06 circuit board work
    [power_board.brd, power_board.sch]
2013-11-06 board work
    [power_board.sch]
2013-11-14 circuits and charger plans
    [power_board.sch]
2013-11-15 circuit boards
    [battery_board.sch, distribution_board.sch, full_power_board.sch]
2013-11-15 board for circuit
    [battery_board.brd]
2013-11-15 various dxf formats for the eagle
    [assbot_logo-circuit_dxf2004.dxf, assbot_logo-circuit_dxf2007.dxf, assbot_logo-circuit_dxf2010.dxf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]
2013-11-15 logo in eagle library
    [assbot_logo-circuit.dxf, assbot_logo-circuit_dxf2004.dxf, assbot_logo-circuit_dxf2007.dxf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]
2013-11-15 battery board made
    [battery_board.brd, battery_board.sch]
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2013-11-16 general update of drawings
    [20130808_AssBot-Mechanical.dwg]
2013-11-16 new board and some ignores
    [distribution_board.brd, distribution_board.sch]
2013-11-17 gittin the night away
    [battery_board.brd, battery_board.sch, distribution_board.brd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]
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2013-12-02 first board finished
    [battery_board.brd, battery_board.sch, distribution_board.brd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]
2013-12-02 fixed board error
    [battery_board.brd, battery_board.sch]
2013-12-02 Revert "fixed board error"
    This reverts commit a9d72898da9c7dfbc8182aee948ad086d6644fb1.
    [battery_board.brd, battery_board.sch]
2013-12-02 new switch and fuse circuit
    [switch-fuses.brd, switch-fuses.sch]
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2013-12-04 more datasheets
    [switch-fuses.brd, switch-fuses.sch]
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2013-12-17 made board tracks bigger
    [battery_board.brd, switch-fuses.brd]
2014-01-05 new shit
    [battery_board.brd, distribution_board.brd, switch-fuses.brd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]
2014-01-28 Trying to debug network communication, seems to be an motors.ipc issue
    [srv_motors.py, srv_remotecontrol.py, test_remotecontrol.py]
2014-01-28 debugging network communication
    The ps2 controller and arduino (freetronics) are talking over the
    network and the message is getting to the robot via the cherrypy
    webserver. The message doesn't seem to be getting passed through the
    motors.ipc to the motors server... They are receiving a message of 0...
    [RemoteControl.ino]
2014-02-15 fixed motor code - acceleration value problem
    [srv_motors.py]
2014-02-18 fixed motor code
2014-03-23 fix problems with the dead band
    [srv_remotecontrol.py]
2014-03-23 fixed motor controller directions
    [srv_remotecontrol.py]
2014-03-23 increased the central deadband to prevent jerky movement at rest...
    [srv_remotecontrol.py]
2014-03-24 Create sensor-mounting-bracket.stl
    Trying to design a 3d printable model that can slip over the aluminium extrusion in order to mount sensors at any location around the extremity
    [sensor-mounting-bracket.stl]
2014-03-24 3d sensor clip
    [front_sensor_clip_mount.dwg, front_sensor_clip_mount.stl]
2014-03-24 corrupted file
    [sensor-mounting-bracket.stl]
2014-03-24 revised thing
    [front_sensor_clip_mount2.stl]
2014-03-25 Unable to be loaded into MakerWare
    [front_sensor_clip_mount.stl, front_sensor_clip_mount2.stl]
2014-03-25 Minor hole adjustments
    [front_sensor_clip_mount.dwg]
2014-03-25 3d design of a 45 degree sensor mount
    [front_sensor_clip_mount.dwg, front_sensor_clip_mount45.dwg]
2014-03-25 minor change to reduce deformities on clip
    [front_sensor_clip_mount45.dwg, front_sensor_clip_mount45.stl]
2014-03-27 built some shit for main power panel
    [assbot_logo-outline-small.dxf]
2014-04-02 more ass-work done
    [IR-Ultrasound-mount.skp, IR-mount-left45.skp, IR-mount-right45.skp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]
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2014-04-04 new fan clip design
    [Fan_Clip.dwg, Fan_Clip.stl]
2014-04-04 git is stuffed
    [Fan_Clip.dwg, front_sensor_clip_mount45.dwg]
2014-04-04 test spring for test print
    [Sprung_test_print.dwg, sprung.stl]
2014-04-04 Updated to fit within print area
    [Sprung_test_print.dwg, sprung.stl]
2014-04-05 more parts to print... jump on the band wagon!
    [20-210-M4-Extrusion.stl, Sprung_test_print.dwg, sprung_mk2.stl]
2014-04-06 Ride that horse
    [Sprung_test_print.dwg, sprung_mk2-1.stl]
2014-04-06 connector for extrusion
    [20-M4-connector.stl]
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2014-04-06 Trying to debug zmq subscribe problem - added extra debug info
    [srv_irdist.py, test_irdistance.py]
2014-04-11 using tcp for zmq as workaround
    [srv_irdist.py, srv_motors.py, srv_remotecontrol.py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]
2014-04-14 git. git git gitgit. git
    [12mm-square-quadangle.skp, 12mm-square-tripleangle_left.skp, 12mm-square-tripleangle_left.stl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]
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2014-04-17 reverted tcp changes, problem seemed to be file permissions
    [srv_irdist.py, srv_motors.py, srv_remotecontrol.py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]
2014-04-30 prototype drawings
    [base-prototype.skp, base-prototype.stl, body-frame-scaled.skp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]
2014-05-01 added js gauges and fixed file references
    [srv_remotecontrol.py]
2014-06-24 pan tilt mechanism for micro servos
    [PanTilt.dwg, PanTilt_Base.stl, PanTilt_Rotor.stl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]
2014-06-26 Updated model after first print
    [PanTilt.dwg, PanTilt_Base.stl, PanTilt_Rotor.stl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]
2014-06-27 minor modifications after 2nd print
    [PanTilt.dwg, PanTilt_Rotor.stl, PanTilt_Stator.stl]
2014-07-09 linbus circuits
    [injector.brd, injector.sch]
2014-07-12 Poorly Rooted V1
    [injector.brd]
2014-07-13 45degree joint bracket for body work
    [corner_join_45.FCStd, corner_join_45.stl]
2014-07-16 LED board for pig head
    [pig_led.brd, pig_led.sch]
2014-07-17 pig skull led board complete
    [pig_led.brd, pig_led.sch]
2014-07-19 pig head temporary brackets
    [body-frame-scaled.skp, skull_bracket_back.stl, skull_bracket_front.stl]
2014-07-22 created a mirror on the wall
    [corner_join_45_Mirror.stl]
2014-07-23 3d printer calibration objects
    [Calibration.stl, Calibration2.stl]
2014-07-24 test mounting plate for shafting
    [Top_Plate_Concept.dwg, Top_Plate_Concept_L_Bottom.stl, Top_Plate_Concept_R_Bottom.stl]
2014-07-27 added some extra brackets to join the frame
    [FrontFrameBrackets.dwg, corner_join_33.stl, corner_join_56.stl]
2014-07-27 Cover Pieces for laser cutting c/o Louise
    [Cover Pieces.dwg]
2014-08-06 switch brackets
    [Corner_pair-36deg.stl, Cover Pieces ACAD2010.dwg, Cover Pieces.dwg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]
2014-08-11 3d model for snap dragons
    [SnapMagnet.dwg, SnapMagnet_Cork.stl, SnapMagnet_Goofy.stl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]
2014-08-11 modifications after print to better fit frame
    [SnapMagnet.dwg, SnapMagnetV2_Goofy.stl, SnapMagnetV2_Normal.stl]
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2014-10-06 refined drawing for full size template
    [Top_Plate_Concept.dwg]
2014-10-07 Redraw of pan tilt for metal fabrication
    [PanTilt_Metal.dwg]
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2014-11-01 top plate platters for machining
    [Top_Plate_Concept.dwg]
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2015-01-25 trying to get servo control working - no errors
    [lib_pololu.py, srv_remotecontrol.py, test_servos.py]
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2015-02-07 trying to get battery voltage messages passed to webpage, replaced tabs with spaces
    [srv_battery.py, srv_remotecontrol.py]
2015-02-07 fixed battery status json
    [srv_remotecontrol.py]
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2015-02-09 moved time on battery calc to odroid to avoid time zone diffs
    [srv_battery.py]
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2015-02-20 fixed problems with recv_json hanging/ waiting for a message
    [test_remotecontrol_flask.py]
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2015-04-02 removed code that might prevent ip being displayed on next start up
    [srv_irdist.py, srv_lcd.py]
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2015-05-10 fixed bugs in srv_shaft/ updated IR to remote open/ tweaked config
    [srv_irdist.py, srv_shaft.py, test_relays.py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]
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2015-06-06 new switch holder. longer delay on ultrasound arduino code
    [switch-holder.skp, switch-holder.stl]
